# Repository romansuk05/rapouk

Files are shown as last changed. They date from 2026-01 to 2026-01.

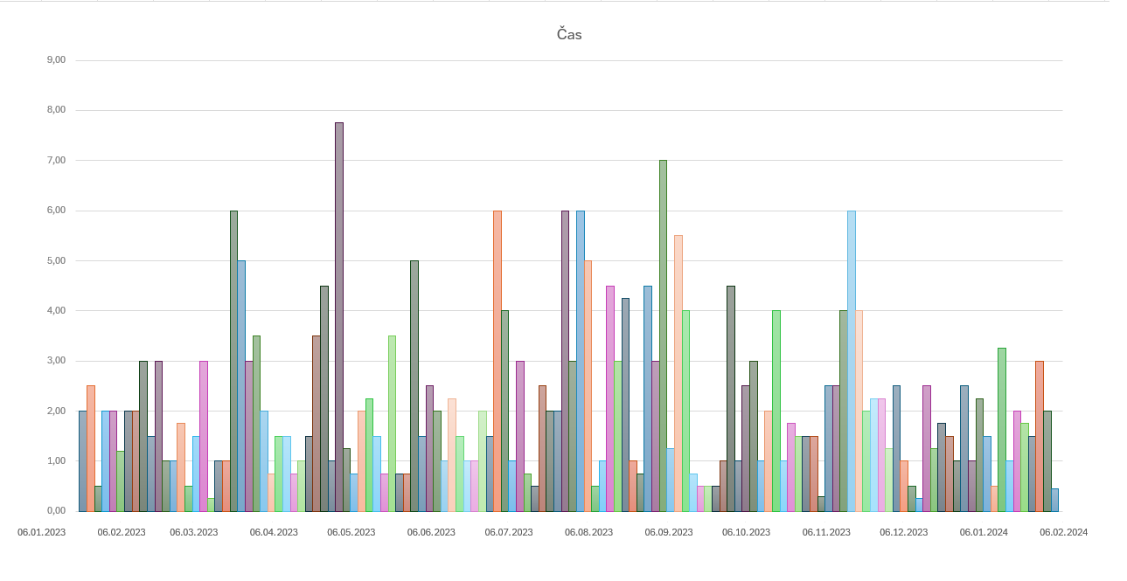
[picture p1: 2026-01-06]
Datasheet and pics/Graf.png

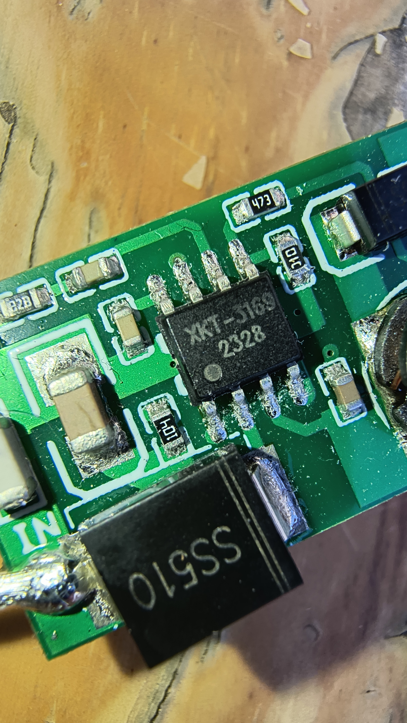
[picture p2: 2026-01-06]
Datasheet and pics/IMG_20240922_112600092_HDR.jpg

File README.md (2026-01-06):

<h1>Project Rapouk</h1>

<p>Hello, this project I made on highschool as final project. Rapouk is quadruped robot. I made it from aluminium on DIY mill, ESP32 and custom PCB. There should be everything which you should need for assembling your Rapouk. Evethought everything is in czech language, so use some translator for this xD</p>
<p>Also there are my thesis with everything that I done in this project</p>
<p>This depo is unsorted af so GL&HF with finding something xD</p>
<p>It is completly open source, so create another versions of this spider</p>
<p>There are some interesting links with this project:</p>
<p>https://www.youtube.com/watch?v=WBYnp2NAGiE</p>
<p>https://www.instagram.com/romansuk05/reel/DLpOciDirai/</p>

<p>Enjoy your journy with Rapouk!</p>





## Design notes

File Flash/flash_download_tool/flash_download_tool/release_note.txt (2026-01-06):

3.9.8：
* add UI to support flash & efuse read
* support ESP32-C5 / ESP32-C61

3.9.7：
* support ESP32-P4
* update UI display icon
* Fix bug: icon stuck after long-term use

3.9.6：
* support ESP32/ESP32H2/ESP32C6/ESP32C2/ESP32S2 secure boot version2 and flash encryption
* config DUT number in multiconfig file ,up to 20pcs
* update secure config file, see docs in detail

3.9.5：
* support esp32-h2
* support erase button disable
* fix some bugs

3.9.4：
* support esp32-c6
* support esp32-c3/esp32-s3 flash encrytion
* add xmc flash fix
* support dut count in factory mode

3.9.3:
* support esp32-c2
* update finish UI show

3.9.2:
* fix configure file error
* update autostart process

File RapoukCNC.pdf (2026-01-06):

Vyšší odborná škola, Střední průmyslová škola a Obchodní akademie,

### Čáslav, Přemysla Otakara II. 938

# ROČNÍKOVÁ PRÁCE

2024 | Roman Suk

Vytvoření základní konstrukce robotického pavouka včetně dokumentace a vizualizace.

Čestné prohlášení

Místopřísežně prohlašuji, že jsem svou ročníkovou práci vypracoval samostatně a použil

jsem pouze podklady (literaturu, projekty, SW atd.) uvedené v seznamu vloženém v práci.

Prohlašuji, že tištěná verze a elektronická verze práce jsou shodné.

V | , dne | | |
| podpis

Poděkování

Děkuji vedoucímu práce Ing. Františkovi Obešlu a oponentovi práce Ing. Janu

Novákovi. Dále Mgr. Karlu Kvapilovi, Bc. Matěji Reichmannovi, Ing. Karlu

Mlčochovi, Ing. Vlastimilovi Andrlemu a v neposlední řadě i třídnímu učiteli Ing.

Davidu Němcovi MBA, a zejména svým rodičům za obětavou pomoc a podnětné

připomínky, které mi během práce poskytovali.

Anotace

Cílem této práce bylo vytvořit konstrukci robotického pavouka. V průběhu práce probíhal

výpočet a výběr materiálu. Práce se dále zaobírá stavbou CNC stroje, svařováním hliníku

a skládáním pavouka samotného.

Klíčová slova

Robotika, pavouk, konstrukce, hliník, CNC, programování, sváření

Annotation

The main focus of this coursework was to create body of robotic spider. There was

materiál selection and calculation. Next focus was building of the CNC machine,

aluminium welding and assembly of the spider itself.

Keywords

Robotic spider, construction, aluminium, CNC, programming, welding

## Obsah

## 1 Úvod

V dřívějších dobách, kdy jsem si hrál s RC modely, mě mrzela jedna věc a to, že ke

každému modelu byl potřeba přesný ovladač. Dražší modely už měly univerzální, ale ty

jsem neměl. Občas ani nebyla možnost, v případě ztráty nebo rozbití ovladače,

komunikační jednotku vyměnit.

Největším paradoxem je, že dnes všichni disponujeme univerzálními ovladači, se kterými

se lze připojit k internetu. Ano – telefon, tablet, nebo i počítač. Tak proč nevyužít tyto

technologie?

S tímto mě vždy fascinovaly neobvyklé platformy robotů. Kreativita, projekt, mechanika

a vše, co za těmito speciálními projekty stálo. Z toho důvodu jsem zvolil platformu

pavouka. Vybral jsem si pavouka se čtyřma nohama, protože má menší počet

servomotorů a baterie bude mít delší výdrž. Nadále jsem měl myšlenku, zda se bude můj

„pavouk“ pohybovat jako pavouk (tělo je při pohybu ve stejné výšce), nebo jako klasické

čtyřnohé zvíře, co svým tělem kolíbá.

Celý projekt jsem pojmenoval pod názvem Rapouk. Název vznikl spojením slov robot a

pavouk.

## 2 Prvotní konstrukce

Tento projekt jsem chtěl vytvořit již před lety. Z toho důvodu už jsem měl vytištěné 3D

modely z internetu. Bohužel už nejsem schopen najít zdroj, odkud jsem v té době čerpal.

V úložném boxu s různými 3D modely jsem našel tyto vytištěné součásti a použil je pro

prvotní seznámení s pohybem.

## 2.1 Programování pavouka

První nápad mě inspiroval v přírodě. Zanalyzovat videa pavoučích pohybů a vytvořit

stejné pohybové algoritmy, které nám jsou dostupné ve volné přírodě. Bohužel v přírodě

neexistuje žádný pavouk se čtyřma nohama.

Vycházel jsem z videí různých pohybů těchto pavouků na internetu. Následně jsem si

vytvořil vlastní algoritmy pohybů, se kterými budu vylepšovat finální model. Nechtěl

jsem nejdříve modelovat a následně programovat, protože jsem nevěděl, na které

problémy narazím. Tento krok mi ušetřil mnoho času a pomohl mi s vylepšením budoucí

konstrukce (viz Tření). (1) (2) (3) (4) (5)

## 2.2 Tření

Při prvním vytváření algoritmů jsem narazil na problém se třením. Na hladkém stole, na

kterém pracuji, konstrukce vysloveně klouzala. Nedokázala se hýbat, protože měla

nízkou hmotnost a nevytvořilo se dostatečné tření, aby se rozpohybovala. Při tomto

testování byla konstrukce z ABS plastu.

## 2.3 Výpočty

V rámci této práce jsem prováděl výpočet zatížení na ohyb v MS Excel. Počítal jsem

nestandartním způsobem, kdy počítám s redukovaným maximálním napětím. To

znamená, že využívám určité procento maximálního napětí, čímž dochází

k předimenzování. Vyšlo mi, že při 10 % maximálního napětí na ohyb servomotor udrží

12,5 N neboli 1,25 kg (viz Příloha EE). Využíval jsem data z datového listu od

servomotoru SG90 9 g, který má vytvořená převodová kola z nylonu. (6) (7)

## 3 Tvorba konstrukce

## 3.1 3D tisk

Při vytváření modelů jsem se inspiroval různými konstrukcemi z internetu. Po analýze

nápadů a provedení od ostatních tvůrců jsem začal modelovat svého pavouka. (1) (2) (3)

(4) (5)

Modely, které jsem vymodeloval s přesným rozměrem, jsem vytiskl na 3D tiskárně a

zkontroloval. Zjistil jsem, že z důvodu tepelné roztažnosti, jsou rozměry jiné. U menších

rozměrů (do 5 mm) byl rozdíl 0,3 mm. U větších, číselně (od 20 mm) byl rozdíl okolo

0,7 mm. Model jsem v programu Autodesk Inventor zvětšil o rozdíl, aby vytisknutá část

pasovala přesně do uložení.

Po konzultaci s vedoucím práce jsem zjistil, že se model nerozšiřuje v modelovacím

programu, ale ve sliceru před tiskem. Hodnoty jsem vrátil na původní a vytiskl

standartním způsobem.

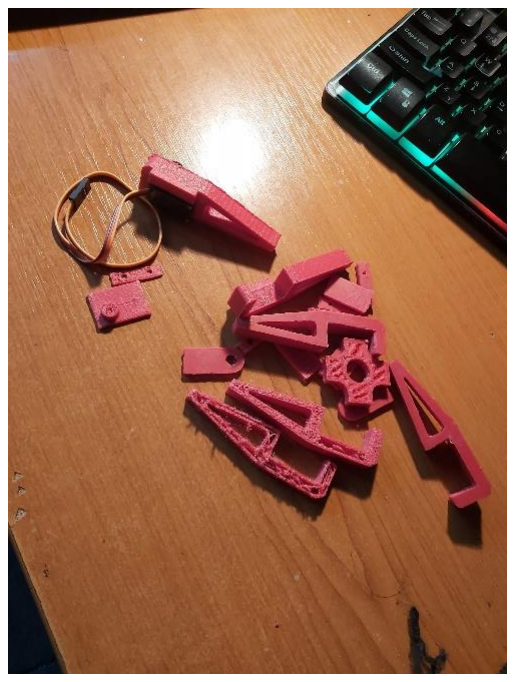
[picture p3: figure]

Obrázek 1 - 3D modely konstrukce

## 3.2 Konstrukce z hliníkové slitiny

Plastové konstrukce jsem tvořil již dříve. Mým hlavním záměrem bylo tento projekt

vylepšit a obohatit o něco nového. Zalíbila se mi myšlenka použití kovů. Vybral jsem si

hliníkovou slitinu – je levná, lehká, dostupná, však složitá na obrábění, pokud nebude

chlazena správnou kapalinou.

Původně jsem chtěl odlévat a použít hliníkové plechovky od sycených nápojů. Po zjištění

komplikovanosti technické dokumentace jsem se rozhodl obrábět z normalizovaného

polotovaru. Zbytečně bych ztrácel čas, protože samotné odlití by nebylo tak časově

náročné jako tvorba technické dokumentace odlitků.

V domácím skladu jsem našel ploché profily o tloušťce 10 mm, 5 mm a 3 mm. Přesně ty,

které jsem potřeboval. Tímto jsem mohl začít obrábět. Jedná se o materiál ENAW-6060

T6 (AlMgSi0,5). Zmíněný materiál má průměrné technologické vlastnosti a lze ho použít

téměř při jakékoliv zpracování. (8)

Obrázek 2 – Polotovary z hliníkové slitiny

Nejdříve jsem si vytvořil rýsovací jehlu, protože v dílně nebyla žádná k nalezení. Vytvořil

jsem ji z kulatého pilníku. Následně jsem nalepil výkres na kovový profil pomocí

klasického lepidla Herkules a začal vše obkreslovat (viz Obrázek 3 - Příprava ručního

obrábění, strana 14).

Připravil jsem si přímočarou pilu s plátkem určeným na hliník a jeho slitiny. Jako první

jsem začal obrábět základní rám pavouka. Ten je určen pro montáž motherboardu,

akumulátoru a dalších potřebných součástí. Strávil jsem nad tím mnoho času s relativně

nepřesným výsledkem. Proto nastal čas nasadit stroje!

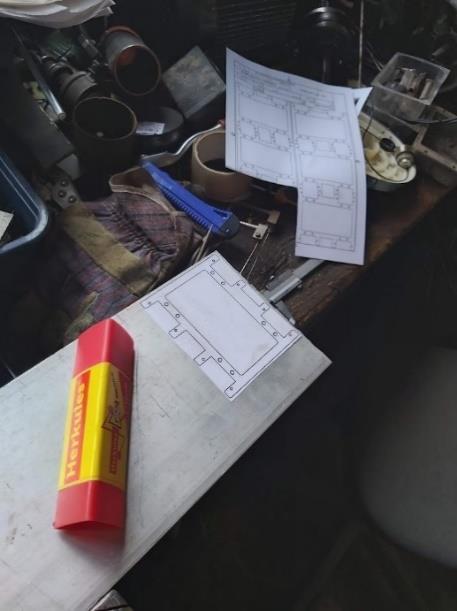
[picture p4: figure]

Obrázek 3 - Příprava ručního obrábění

## 3.2.1 Další materiály

V rámci správné analýzy jsem se rozhodoval i nad ostatními materiály.

### 3.2.1.1 Ocel

Kvůli dobrému obrábění jsem mohl využít ocel. Přesněji pásové nebo plechové

polotovary. Jedna z největších záporných vlastností ocelí je koroze. Proto jsem nad tímto

materiálem dále neuvažoval. Sice všechny faktory splňuje, ale zde musím použít materiál,

který nekoroduje.

### 3.2.1.2 Nerezová ocel

Ocel, která nekoroduje zní jako ideální materiál. I přes vynikající vlastnosti jsem si

nerezovou ocel nevybral, protože bych ji musel nakoupit. Zatímco vybrané hliníkové

polotovary jsem měl ve skladu s plným rozsahem použití a rozměrů.

### 3.2.1.3 Titanzinek

Titanzinek byl pro mě absolutně neznámý materiál. První, co jsem uviděl byla cena, která

byla hodně vysoká. To by mi tento projekt dost prodražilo, proto jsem tento materiál dále

ani nezkoumal.

## 4 CNC

Přiznám se, jsem líný člověk, který si chce vše zjednodušit. Proto jsem začal s opravou

staré CNC frézky, která fungovala ještě na MS-DOS. To jsou doby Windows 95, 98, až

XP. Takže tato frézka je starší, jak většina aktuálních studentů na naší škole (k roku

2023/24).

Obrázek 4 - Ruční obrábění

Začal jsem vyčistěním pomocí stlačeného vzduchu z kompresoru, následně pomocí

navlhčeného kusu látky. Závity s kolejnicemi, na kterých se posouvá fréza, jsem pročistil

a namazal pomocí přípravku WD40 a jeho náhražky od W5. Stroj jsem vyčistil pomocí

čističe na brzdy. Též jsem musel rozebrat a očistit krokové motory, protože rotor byl

přirezlý ke statoru, k čemuž jsem použil brusný papír o hrubosti 240. Následně jsem

vyměnil sloupečky, na kterých je upevněn posuvný motor, ale chyběla jedna věc – u CNC

stroje byla pouze jedna zubová spojka, a proto jsem je musel vyrobit. Celkově jsem

potřeboval čtyři spojky. Použil jsem opět program Autodesk Inventor. Spojky

vymodeloval, vytiskl na 3D tiskárně a pilníkem poupravil, aby fungovaly jako originální.

Ano, mohl jsem zvolit i jiné způsoby, jsem lenošná osoba, a proto jsem nechal výrobu na

dalším CNC stroji.

Obrázek 5 - Nálezový stav CNC frézky

## 4.1 Posuvný vozík na CNC frézku

Celý stroj jsem položil na konstrukci s kolečky, která mi tvořila velice dobrý stůl. Celou

CNC frézku jsem měl v perfektní výšce na čistění a operace. Na spodek konstrukce jsem

provizorně vložil sololitovou desku, abych si mohl odkládat věci.

Díky tomuto vozíku jsem se mohl s celým strojem pohybovat po dílně prakticky

kamkoliv. Též jsem ocenil kolečko se zašlapávací brzdou, aby se stroj nemohl pohybovat.

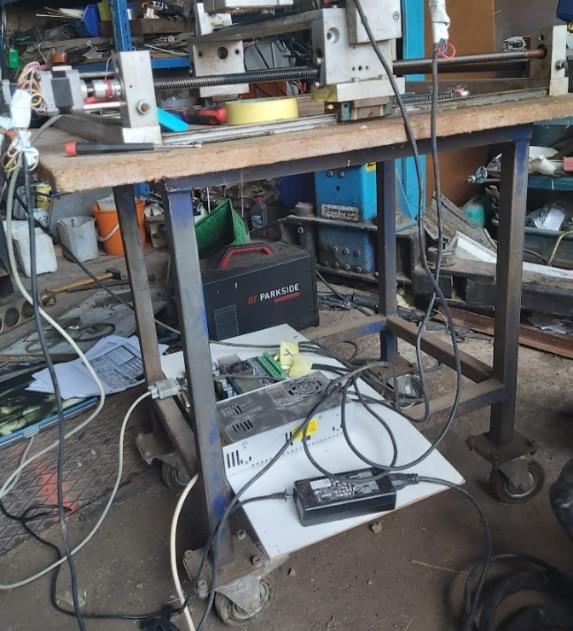
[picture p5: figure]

Obrázek 6 – Provizorně vložená sololitová deska

## 4.2 Elektronika

Původní elektronika byla v plastové krabici, která v sobě měla zdroj, připojení pomocí

LPT a připojení pro krokové motory pomocí sériového portu. Na neštěstí jsem nebyl schopen najít vhodné nastavení, a ani se mi ho nepodařilo vytvořit. Čekala mě výměna

elektroniky. Jako řadič jsem použil čtyřosý řadič TB6560, jenž jsem připojil k 12 V

zdroji, který dokázal pohánět proudem stroj až 5 A. Celkově zdroj dokázal produkovat

60 W elektrické energie. Ke zdroji jsem připojil také připojovací šnůru do zásuvky na

230 V.

Po hodinách zkoušení jsem narazil na stejný problém. Motory vydávaly zvuk, však

nehýbaly se. Hledal jsem a zkoušel různé možnosti nastavení, ale nic se mi nepodařilo

zprovoznit. Takže jsem vyzkoušel ostatní desky s označením TB6560. Mnoho jich

nefungovalo, ale pětiosý řadič začal fungovat. Dokonce jeden řadič shořel.

Vše jsem zapojil, připojil původní ruční ovládání a vše začalo fungovat. Vyzkoušel

všechny osy a nastavil motory na řadiči. Ještě jednou pročistil všechny kolejnice a matice,

které byly znečištěné od dřívějšího používání.

Obrázek 7 – Ilustrační fotka ovládací desky a zdroje

## 4.2.1 Nastavení elektroniky

K mé ovládací desce naštěstí existoval datový list. Tím jsem zjistil nastavení daných

spínačů. V komunitě lidí, kteří se věnují domácím CNC strojům je tato elektronika velice

oblíbená. S hledáním dodatečných informací jsem neměl problém. Především jsem hledal

v manuálu na komunitních stránkách. (9)

Celkově pro jeden krokový motor je jeden DIP spínač se šesti pozicemi.

### 4.2.1.1 Nastavení proudu

Prvními dvěma pozicemi se nastavuje maximální proud pro jednotlivý výstup motoru

ovládací desky. Toto nastavení jsem nastavoval dle zahřívání a výkonu krokového

motoru. Původní motory neměly dostatečný výkon. Při otočení se velice zahřívaly. Přesně

toto nesmí nastat.

Pozice 1 | Pozice 2 | Maximální proud
Zapnuto | Zapnuto | 100 %
Zapnuto | Vypnuto | 75 %
Vypnuto | Zapnuto | 50 %
Vypnuto | Vypnuto | 25 %

Tabulka 1 - Nastavení proudu (9)

Se silnějšími motory jsem využíval 75 % maximálního proudu.

### 4.2.1.2 Nastavení mikrokrokování

Pátou a šestou pozicí se nastavuje rozložení kroku na více menších kroků, tzv.

mikrokroků.

Pozice 5 | Pozice 6 | Rozdělení kroku
Zapnuto | Zapnuto | 1
Zapnuto | Vypnuto | ½
Vypnuto | Zapnuto | ⅛
Vypnuto | Vypnuto | ¹⁄₁₆

Tabulka 2 - Nastavení mikrokrokování (9)

### 4.2.1.3 Nastavení vybíjení

Toto nastavení jsem moc nenastavoval a nechal na základní pozici. Ovládá se třetí a

čtvrtou pozicí DIP spínače.

Pozice 3 | Pozice 4 | Mód
Zapnuto | Zapnuto | Rychlé
Zapnuto | Vypnuto | 25 %
Vypnuto | Zapnuto | 50 %
Vypnuto | Vypnuto | Pomalé

Tabulka 3 - Nastavení vybíjení (9)

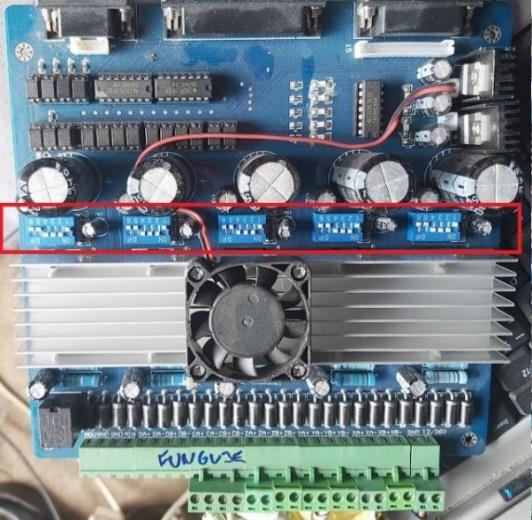
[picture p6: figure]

Obrázek 8 - Nastavení ovládací desky

## 4.3 Vřeteno

Originální vřeteno jsem na stroji neměl. Použil jsem tedy jiné vřeteno na 48 V. Dokonce

k němu bylo i přesné uložení pro tento motor.

Původní uložení na frézce mělo menší rozteč děr, takže bylo potřeba vyvrtat nové díry. Z

důvodu nedostatku místa ze zadní části, kde byl hlavní nosník osy Y, jsem musel vytvořit

závity M6. Do těchto závitů se zašroubovala závitová tyč, která sloužila stejně jako

svorník. Jednalo se o nejjednodušší řešení, protože bych musel frézovat otvory pro

uložení hlavy šroubu s vnitřním šestihranem.

U oceli by to nebyla veliká problematika, ale u hliníkových profilů jsem, z důvodu

nízkých zkušeností, použil tento postup. Dodnes ani nevím, zda ve výbavě mám

záhlubník pro vytvoření otvorů pro hlavu šroubu.

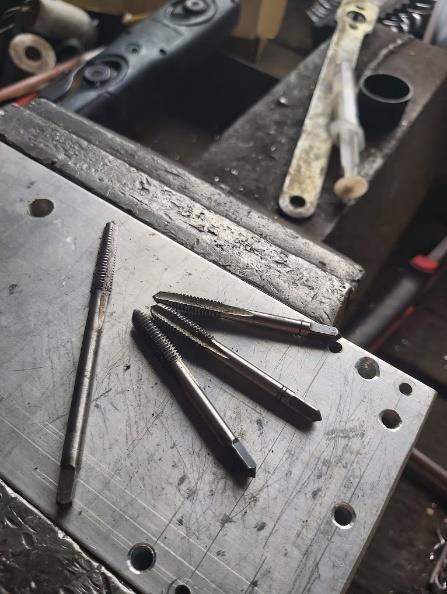
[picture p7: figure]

Obrázek 9 - Závitníky

Závitové tyče jsem zalepil pomocí přípravku Loctite. Na závitové tyče jsem vložil uložení

vřetena, které jsem utáhnul kuželovými maticemi. Tyto matice mi vyrobil otec. Do

sklíčidel vrtačky jsme uchytili závitovou tyč, na kterou jsme našroubovali dlouhou matici.

Matice byla zbroušena na kotoučové stolní brusce. Tím jsme vytvořili kuželovou

charakteristiku.

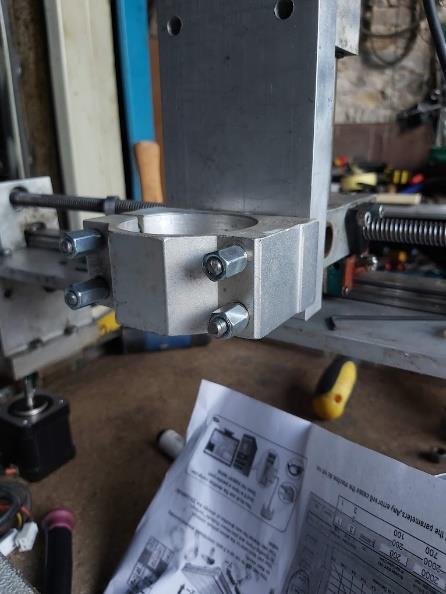
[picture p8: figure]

Obrázek 10 - Uložení vřetena

Kuželovitost jsme využili z důvodu přesného uložení a vycentrování. Díky tomu matice

držely uložení vřetena rovnoměrně.

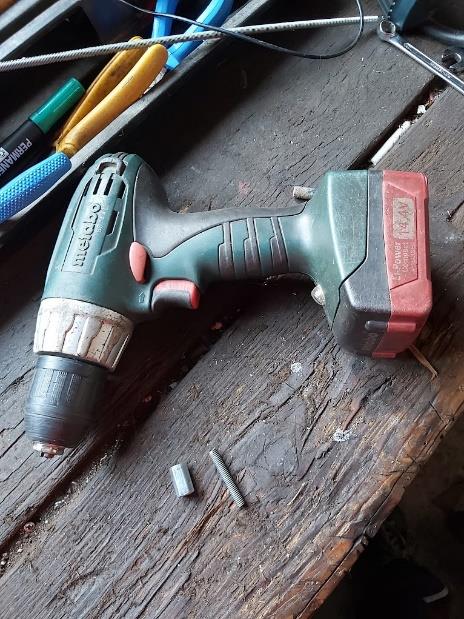
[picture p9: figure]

Obrázek 11 - Výroba kuželové matice

Následně jsem vše připravil a přišrouboval na stroj.

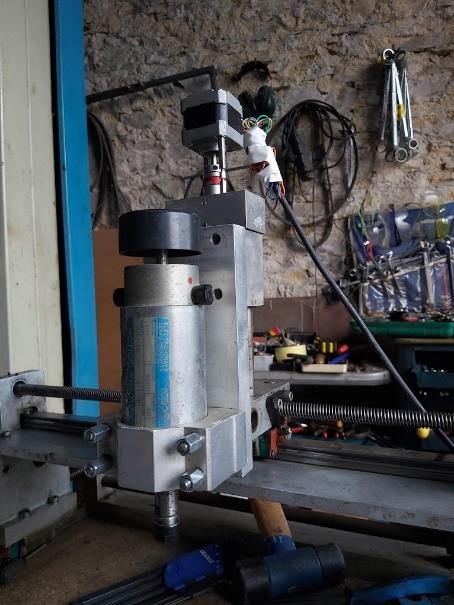
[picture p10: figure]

Obrázek 12 - Vřeteno

## 4.3.1 Kabely k vřetenu

O vřetenu samotném nemám moc informací a špatně se hledají. Neznám ani maximální

proud, a proto musím improvizovat. Ve skladu jsem našel rozebraný podlahový mycí

stroj, který fungoval na akumulátor. Využil jsem silné kabely, které byly dlouhé. Na jeden

konec kabelu jsem připojil konektor pro připojení motoru. Konektor zaletoval a ochránil

smršťující bužírkou vůči zkratu.

Při zkompletování kabelů jsem použil další zdroj na 48 V, ke kterému jsem připojil

přívodní šnůru s ochranou. Ještě jsem použil model ochranné krytky, kterou jsem stáhl

z internetu a vytiskl na 3D tiskárně. (10) Zabraňuje dotyku s 230 V. Teoreticky by zde být nemusela, avšak z vyššího napětí jak 50 V mám obavy, a proto z důvodu bezpečnosti

tuto krytku sem přidávám.

Obrázek 13 - Krytka zdroje

Bohužel při zkoušce pohybu s osami jsem zjistil, že kabely jsou, i přes jejich délku, moc

krátké. Měl jsem dvě možnosti. Najít, nebo koupit jiné, anebo zmenšit vzdálenost mezi

zdroji a krokovými motory s vřetenem. Nejrychlejší řešením bylo zmenšení vzdálenosti.

Obrázek 14 - Krytka upevněna na zdroji

## 4.3.2 Změna polohy řídící části CNC stroje

Potřeboval jsem celou řídící část posunout co nejvýše. Řídící částí míním tu část, která

měla sloužit pro odkládání nářadí (viz Obrázek 6 – Provizorně vložená sololitová deska,

strana 16). Změřil jsem si výšku zdroje, která byla 50 mm. Proto jsem zvolil jako

dostatečnou mezeru 80 mm.

Mezi zbytky materiálu jsem našel L profily s podélnými dírami. Délkově měly přesah

necelých 40 mm. Díry a délka profilu mi přesně vyhovovaly.

Do konstrukce s kolečky jsem vyvrtal díry o průměru 4,8 mm. Předvrtal jsem díru o

průměru 2,2 mm a následně průměr zvětšoval. Vše jsem vrtal akumulátorovou vrtačkou od firmy Metabo. Vzdálenost od horního nosníku byla 100 mm. Profily jsem přinýtoval

pomocí krátkých nýtů s širokou hlavou a použil ruční nýtovací kleště. Ruční kleště mi

daly zabrat, protože drtivou většinu času jsem nýtoval s pneumatickými nýtovacími

kleštěmi.

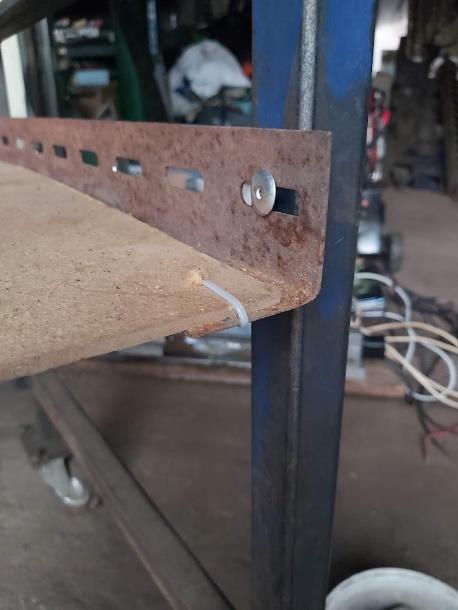
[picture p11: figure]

Obrázek 15 - Přinýtovaný L profil

Nejdříve jsem pracoval se špatnými nýtovačkami, které byly vyrobeny na kratší hřebíky,

a proto se mi zasekávaly a nenýtovaly. Po výměně jsem mohl v nýtování pokračovat.

Bohužel po nýtování se mi hřebíky přetrhly ve špatném místě. Proto jsem vzal silné a

přepákované štípací kleště, kterými jsem tuto nedokonalost vyřešil.

Následně jsem vložil původní sololitovou desku do L profilů. Ještě jsem použil vodováhu,

zda profily nejsou přinýtovaný špatně, popřípadě křivě. Vodováha mi ukázala perfektní

vodorovnost.

Obrázek 16 - Vodováha

Sololitovou desku jsem ještě připevnil ke konstrukci pomocí stahovacích pásků. Nejdříve

jsem vyvrtal díry a následně spojil.

Vše z řídící části jsem rozebral a složil zpět, aby se mi zbytečně nekřížily kabely mezi

sebou. Jako poslední krok jsem kabely seskládal a spojil opět stahovacím páskem ke

konstrukci.

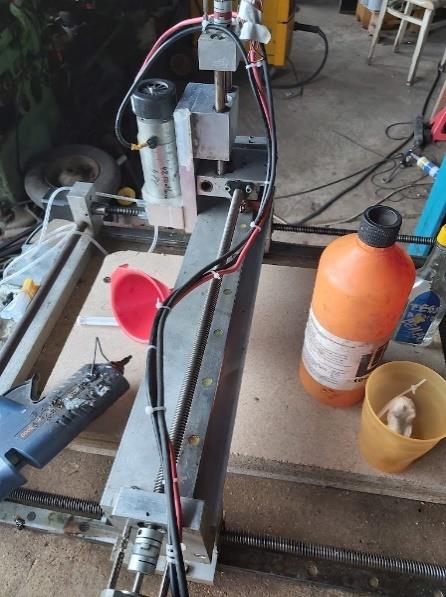
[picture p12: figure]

Obrázek 17 - Osa Y

## 4.4 Motory

Originálně na této frézce byly použity krokové motory Microcom SX17-0804. Na Ose Y

a Z fungovaly dobře, na osu X již nestačily.

Proto bylo potřeba vylepšení s výkonnějšími motory. Použil jsem LDO-42STH47-

1684AS, který disponuje dvakrát větší cívkou.

Obrázek 18 - Krokové motory

## 4.4.1 Uložení motoru

S větším motorem nabývá i samotná váha. Původní uložení, které bylo vytvořeno z

distančních sloupků, by motor neudrželo. Distanční sloupečky jsem odmontoval a využil

vytvořeních závitů ve stavební kostce, kde byl původní motor. Tyto motory měly stejnou

rozteč šroubů, takže zde nebyl žádný problém k vytvoření tohoto uložení.

S tímto uložením přišly první výdaje. Ve skladu jsem neměl tak dlouhé šrouby, které bych

mohl použít na uložení motoru. Proto jsem si nechal objednat šroub s válcovou hlavou a

vnitřním šestihranem M3-60 DIN 912 ZB 8.8, které jsem následně zkrátil na 55 mm.

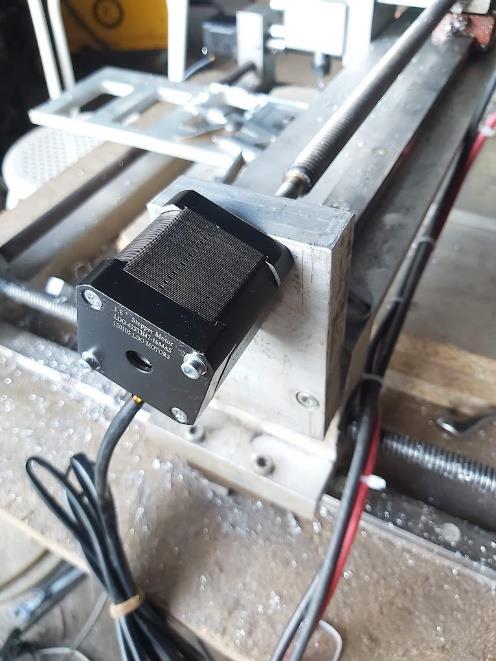
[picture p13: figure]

Obrázek 19 - Krokový motor na ose Y

Při skládání jsem pod hlavu šroubu použil podložku a vše sešrouboval k sobě.

## 4.4.2 Připevnění uložení motoru k nosné desce CNC

## stroje

Připevnit uložení motoru bylo poměrně obtížné. Nosná deska je z dřevotřísky. Jelikož o

stroj nebylo staráno a bylo ve vlhkém prostředí, tak došlo k její deformaci. Naštěstí se

nejedná o velké zkroucení, však o ztrátu pevnosti.

Při připevňování deska nedokázala udržet tlak hlavy šroubu. Pod tlakem hlavy šroubu se

začala drolit a ztrácet pevnost. Z tohoto důvodu jsem použil podložky o velkém vnějším

průměru, abych rozložil tlak při utahování. Tím by hlava šroubu nevytvářela deformace.

Podložky jsem použil M8/9x28-3 mm DIN 440R A2.

Musel jsem vyměnit i samotné šrouby. Původní konstrukce počítala s uložením hlavy

šroubu v nosné desce. Toto uložení jsem nemohl použít. S použitými podložkami šrouby

byly moc krátké. Vyměnil jsem je za delší se stejným průměrem 8 mm neznámé normy.

Celková cena spojovacího materiálu byla 220 Kč včetně DPH.

## 4.4.3 Spojení závitové tyče a motoru

Jeden z mála rozdílů těchto krokových motorů byl průměr hnací hřídele, která z motoru

vycházela. Rozdíl byl u původních 5 mm a nových 6,3 mm. Původní spojení hřídelí bylo

pomocí axiální spojky. Neměl jsem žádné spojky, které by se daly použít. Mohl jsem tuto

spojku koupit, avšak cena těchto spojek, i na východních e-shopech, je vysoká.

S touto spojkou mi pomohl otec. Využili jsme kulatou tyč o průměru 23 mm neznámé

oceli. Tyč jsme uřízli na délku 30 mm a na soustruhu provrtali vrtákem o průměru 6,3 mm

a z opačné strany o průměru 8 mm. Jako pojistné šrouby jsme použili stavěcí šrouby

s vnitřním šestihranem o průměru 5 mm a stoupáním 0,8 mm.

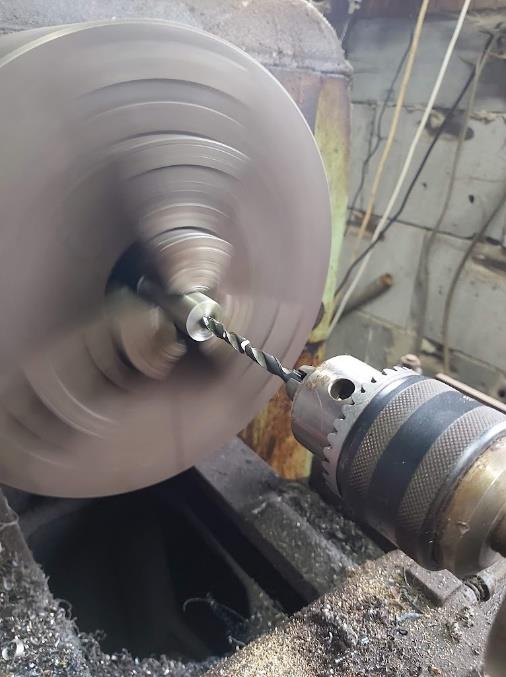
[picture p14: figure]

Obrázek 20 - Soustružení

Spojky jsme nainstalovali na stroj a svoji funkci plnily stoprocentně. Nejdříve jsem se

obával špatného vyvážení nebo vyvrtání spojky. Kdyby spojení nebylo v ose, mohlo by

dojít ke špatnému posuvu stroje.

Tímto bodem byla HW část CNC stroje hotová.

Obrázek 21 - Spojka na ose X

## 4.5 Nástroje pro obrábění

Fréz jsem za život měl v rukách poměrně málo, natož na hliníkové slitiny. Drtivá většina

těchto fréz má průměr okolo 2 mm. Tento průměr je dost malý a to nepočítám, že toto

jsou mé první zkušenosti s CNC frézkou. Bohužel i průměr sklíčidla je malý a to pouze

3,125 mm (3 a ⅛ mm).

Jsem začátečník a v budoucnu nepřepokládám, že budu denně obrábět pomocí fréz.

Z tohoto důvodu jsem se rozhodl nakoupit levné frézy. Objednal jsem je z čínského webu

www.aliexpress.com. Celkově pět fréz na hliník o zmíněném průměru.

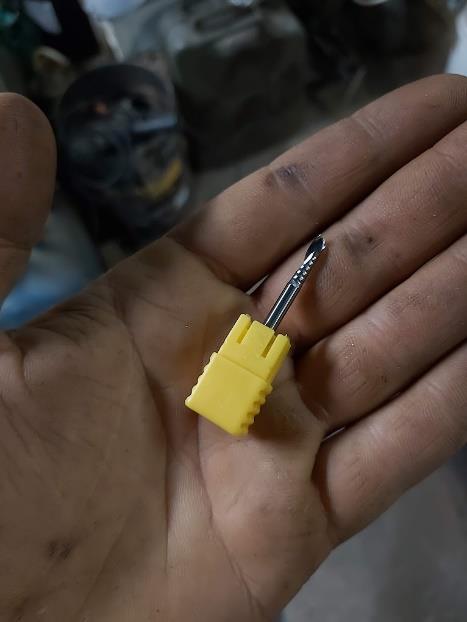
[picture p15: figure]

Obrázek 22 - Fréza o průměru 3,175 mm

Cena těchto fréz byla 16,7€ (necelých 400 Kč) včetně dopravy a DPH.

## 4.6 Testování a kalibrace stroje

Po složení CNC stroje nezbývá nic jiného než testovat. Tato část je důležitá kvůli

samotnému chodu stroje. Při testování jsem zpozoroval, že se stroj lehce zasekává.

Především na ose X, kde jsou uloženy dva motory. Snažil jsem se tento problém vyřešit

zvýšením maximálního proudu. Tímto krokem motory byly hlasitější a vytvářely více

tepla. Proto jsem nastavení vrátil zpět na 50% maxima.

Obrázek 23 - Finální CNC frézka

## 4.6.1 Mazaní

Jedno z dalších řešení nízkého výkonu motorů je mazání. Mazáním lze vytvořit na film,

kterým lze docílit snížení třecí síly na povrchu namazaných částí. Tímto jevem získáme

nižší energetickou náročnost.

K vyčištění jsem používal přípravky WD40 a přípravek na mazaní od W5. Nevýhoda

těchto přípravků je v odpařování. Proto jsem pro dlouhodobé mazání použil grafitovou

vazelínu. Ta se používá prakticky kdekoliv. Osobně jsem se setkal i s mazáním pásů u

rypadla.

Obrázek 24 - Maznice s vazelínou

Vazelínu jsem aplikoval pomocí maznice ve vozících na kolejnicích, které vozí a

podepírají osy. Na závitové tyče jsem použil též grafitovou vazelínu s Interflonem.

Obrázek 25 - Interflon

## 5 Ovládací CNC SW

Dnes je drtivá většina obráběcích SW s licencí. Samozřejmě výjimka potvrzuje pravidlo

a jsou tu i programy, které jsou zdarma a pro “hobby“ použití. Jejich největší nevýhodou

je zastaralost, protože byly vytvořeny v dobách od MS-DOS až po Windows XP. Též je

potřeba počítač s LPT portem, který je velikou vzácností. Tento port se dnes nevyužívá.

## 5.1 Mach3

Mach3 je program volně ke stažení, který lze používat na OS Windows 95 až Windows

XP. Je velice jednoduchý na ovládání, přestože je lehce nepřehledný.

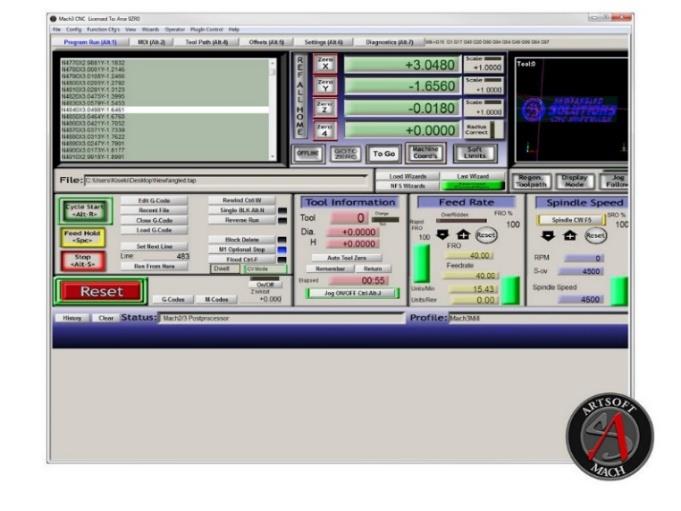
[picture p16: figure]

Obrázek 26 - Mach3 (11)

Bez dokumentace k řídící desce prakticky nelze program použít. Počítač, který skrze LPT

port ovládá CNC stroj, vysílá pulzy na dané piny. Bez správného nastavení pinů nepřijde

informace na určité místo a stroj nebude fungovat. (12)

Následně po nastavení komunikace se musí nastavit motory. Je zde celkově pět políček

pro nastavení.

## 5.1.1 Step per

Step per nastavuje počet kroků krokového motoru na otáčku. Jednoduchým výpočtem si

dokážeme krok na otáčku vypočítat. Tento výpočet lze aplikovat pouze na pojezdech na

závitových tyčích. Pokud by se pro pohyb použily řemeny, tak výpočet bude jiný.

počet kroků na otáčku ⋅ počet mezikroků stoupání

= step per

Rovnice 1 - Výpočet step per (13)

Počet kroků na otáčku vypočítáme pomocí úhlu na krok. U mého krokového motoru je to

je 1,8°.

360

o
1,8

o = počet kroků na otáčku

360

o
1,8

o = 200

Z rovnice lze usoudit, že pro jednu celou otočku musí motor udělat 200 kroků.

Stoupání je myšleno stoupání na závitové tyči, na které se celá osa unáší. Na mém stroji

byly závitové tyče se stoupáním 5 mm.

Mezikrok nám rozděluje samotný krok na více kroků, takzvaných mezikroků. Mezikroky

zvýšíme rozlišení stroje, takže bude větší přesnost a plynulost. Nevýhoda mezikroků je

vyšší spotřeba energie.

200 ⋅ 8
5

= 320

Z dosazení do vzorce vidíme, že do kolonky „Step per“ zadáme hodnotu 320. Tento

vzorec jsem odzkoušel a stroj jsem nechal zkalibrovat v SW. Vše vyšlo přesně dle

výpočtů.

## 5.1.2 Rychlost a zrychlení

Velocity je maximální rychlost, kterou se motor bude pohybovat. Acceleration je

akcelerace motoru. Tímto nastavujeme pohyby krokových motorů. Jednotky se udávají

v mm×s

-1
a mm×s

-2

V programu vidíme křivku zrychlení a zpomalení, která se jmenuje rampa. Program ještě

dopočítává přetížení v jednotce G.

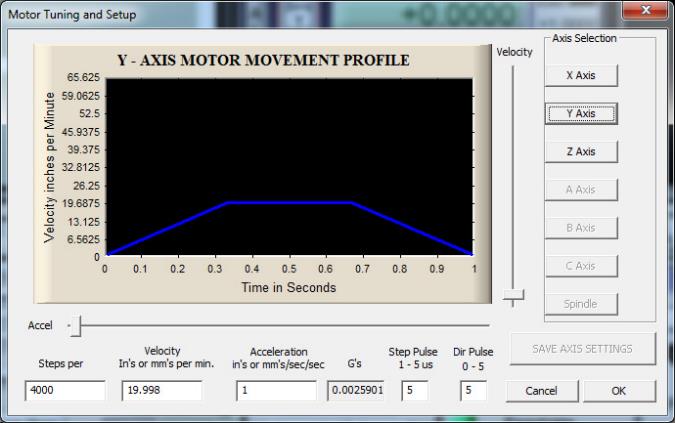
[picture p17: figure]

Obrázek 27 - Mach3 rampa (14)

Při poslechu jiných CNC strojů slyšíme identické pískání a bzučení krokových motorů.

Tohoto zvuku chceme při nastavování docílit.

## 5.1.3 Step a Dir puls

Tyto hodnoty nám nastavují minimální puls, který dokáže řadič zachytit. Toto nastavení

jsem nechal na základním nastavení.

## 5.1.4 Problematika komunikace nových OS

Program jsem nejdříve vyzkoušel na novějším systému Windows 7. Po nízkých desítkách

hodin se mi stroj nepodařilo zprovoznit. Fungoval velice slabě na nesmyslné nastavení

(viz Step per, strana 30). Po uložení nastavení se ukončila komunikace.

Celý problém byl v operačním systému. Používal jsem Windows 7, namísto XP a starších.

Přesně nevím, jakou změnu Microsoft udělal s LPT porty. Kdybych chtěl používat

novější OS, tak bych musel použít převodník za nízké tisíce korun. Proto byla lepší

možnost přeinstalovat počítač na starší verzi Windows.

Po nainstalování Windows XP vše fungovalo. Celý stroj mi fungoval prakticky hned.

## 5.2 Step-Four

Step-Four je program, který se používal už na základním MS-DOS. S MS-DOS mi

pomohl otec, který v DOS dříve pracoval. K jeho zprovoznění bylo potřeba přihlášení s

hardwarovým klíčem, který odesílal data do CNC stroje. Stejně jako Mach3 byl připojen

pomocí LPT portu.

Tento program jsem si moc neozkoušel, protože mi jako první začal fungovat Mach3.

Každopádně prostřední S4 bylo velice retro. Typický retro kostičkovaný design jako mělo

logo od MS-DOS.

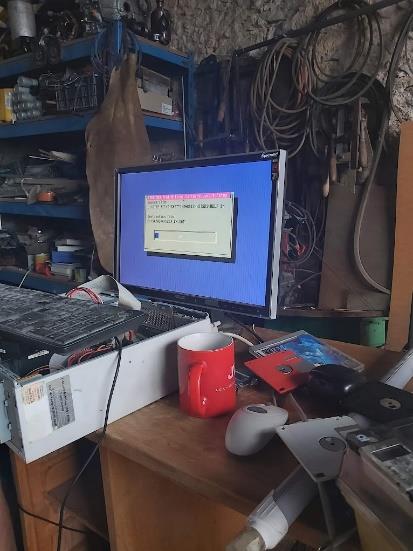
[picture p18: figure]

Obrázek 28 - MS-DOS

## 6 CAM

CAM je nedílná součást CNC strojů, pokud nechceme psát program ručně. Jelikož mi

přijde nesmyslné, abych G-kód psal ručně, tak půjdu touto cestou. Myslím si, že do

budoucí praxe mi tento postup jedině pomůže, a hlavně urychlí celý projekt.

## 6.1 Inventor CAM

První nápad byl Inventor a jeho vlastní CAM. Přeci jenom mám modely vymodelované

právě v tomto programu a v hodinách v rámci zaměření CNC jsem se s tímto CAM

programem učil. Logicky jsem si vyvodil, že by to neměl být problém.

Po různých pokusech jsem došel k závěru, že tento CAM je až moc silný nástroj na

domácí CNC frézku. Má neuvěřitelné možnosti obrábění, které jsou v mém případě

zbytečně složité. Proto jsem začal hledat další CAM.

## 6.2 Lazycam

Jako hlavní SW k frézce používám Mach3. Od firmy Artsoft existuje Lazycam, který je

prezentován právě k Mach3. Jeho hlavní výhoda je jednoduchost, protože vychází

z univerzálních DXF souborů. V tomto programu je možné zadat výkres a přiřadit výšku

polotovaru. Tím se vše zjednodušuje.

Věřím, že mezi sebou pracují dobře, jenže jsem se nedokázal dostatečně rychle

zorientovat v ovládání tohoto programu. Proto jsem zkusil mé štěstí a hledal další možný

CAM s nulovými náklady.

## 6.3 Estlcam 11

Tento CAM jsem našel v seznamu free frézovacích CAM programů. Prostředí z fotek

vypadlo natolik jednoduché, že jsem to nemohl tuto možnost nevyzkoušet. Stejně jako

Lazycam podporuje formát souborů DXF. Všechny parametry včetně řezných podmínek,

pohybů a samotného frézování se zadávaly jednoduše bez větších obtíží. Program je

velice jednoduchý a intuitivní.

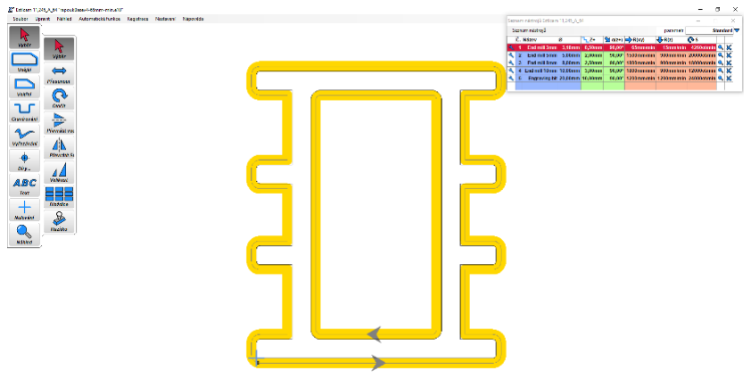
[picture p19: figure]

Obrázek 29 - Estlcam 11

Jediná jeho nevýhoda je počítadlo při spuštění. Dle napočítaného počítadla se zvedá čas

exportu, aby si uživatel musel koupit licencovanou verzi. Tento nedostatek kompletně

ignoruji, protože tento CAM je pro mé účely geniální. Proto tento program budu nadále

používat pro tvorbu G-kódů.

## 6.3.1 První frézování

Jako testovací materiál jsem si vybral to nejsložitější, co mohu obrábět, hliníkovou slitinu. Vše jsem chladil technickým lihem. Úspěšně jsem vyfrézoval první kapsu bez zlomení

nástroje. Samozřejmě jsem spočítal řezné podmínky, abych šanci tohoto neúspěchu

prakticky eliminoval (viz Příloha EE). Všechny výpočty jsem počítal v MS Excel. V této

situaci jsem nevěděl, co mě ještě čeká.

## 7 Chyby CNC frézky

Při každém vývoji se vždy objeví nějaké chyby, právě ty potkaly i mě.

## 7.1 Špatné rozměry

Když jsem vyfrézoval první kapsu v součásti, kterou jsem potřeboval na finální výrobek,

tak jsem nekontroloval rozměry. Počítal jsem s tím, že Mach3 frézku ovládá správně.

Po frézování vnější části konstrukce jsem narazil na tento problém. Křivky, které byly

naprogramovány, byly úplně jiné. Rozměry neodpovídaly a drážka nebyla ani rovná.

Nakonec stroj vyrobil kompletní nesmysl.

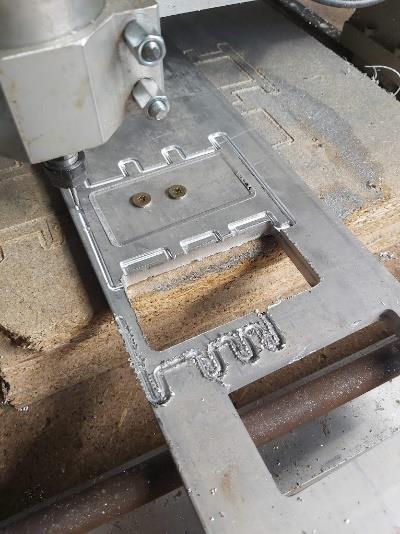
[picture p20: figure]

Obrázek 30 - Nepovedené obrábění na CNC

Problém mohl být jak v HW, tak i v SW. Ze začátku jsem nevěděl, čím by to mohlo být.

Proto jsem zkusil ten samý objekt vyfrézovat do dřeva. Výsledek byl perfektní. Tímto

jsem vyloučil problém ve stránce SW a začal hledat chybu ve frézce samotné.

Jako další test jsem chtěl vyfrézovat čtvercovou kostku o 10 mm. Výsledek místo těchto

rozměrů v ose X a Y byl rozdílný. Přesněji v ose X o 0,7 mm a v ose Y až o 1,5 mm.

Tento test mi ukázal, že krokové motory, nemají dostatečný výkon. Zmenšil jsem řeznou rychlost z 80 mm×min⁻¹

na 65 mm×min⁻¹
. Bohužel tato změna nijak tento problém

nevyřešila. Poslední, kde by mohl být problém jsou samotné motory.

## 7.2 Vylepšení motoru

Na ose Y jsem nechal přimontovaný původní krokový motor. Proto jsem použil stejný

pracovní postup jako při vylepšování motorů (viz Motory, strana 24). Dle výsledků z 10

mm kostky vidíme, že i osa X, která byla vylepšena, taktéž neodpovídá. Proto jsem na

řídící desce přidal maximální proud z 50 % na 100 %. Přestože se to může zdát jako velký

skok, tak jsem postupoval postupně. Při 100 % se krokové motory lehce zahřívaly. Lehké

zahřívání těmto motorům nijak nevadilo.

## 7.3 Nekolmá podložka

Při frézování jsem viděl, jak materiál zabírá do větší hloubky, když se pohybuje po ose

Y. To znamená, že obrobek není kolmo k vřetenu. Tento problém nemohu vyřešit. Mohl

bych vytvořit novou podložku, například stůl s drážkou ve tvaru “T”, avšak to by bylo

velmi časově i finančně náročné.

Jelikož jsem pracoval pouze ve 2,5D obrábění, tak jsem zvýšil nulový bod v ose Z. Tím

bych zmenšil hloubku záběru v první vrstvě. Ostatní vrstvy by se frézovaly stejně. Jiné

řešení jsem neměl.

## 7.4 Kontrola dotáhnutí šroubů

Jelikož nekontroluji, a ani neznám správné utahovací momenty, na které se mají stavěcí

šrouby dotahovat, tak občas se nějaký povolí. Toto se mi stalo uprostřed frézování kloubu.

Naštěstí se nástroj nezlomil. Pouze jsem přišel o kus materiálu.

## 7.5 Free verze Mach3

V průběhu frézování jsem zjistil, že free verze SW dokáže pracovat s G-kódy maximální

do 500 řádků. Nejdelší G-kód, který jsem naprogramoval, měl 1150 řádků. Z tohoto

důvodu jsem musel G-kódy rozdělovat podle pořadí operací. Musel jsem vymazat přebývající mezery a nepotřebné příkazy. Naštěstí se největší součást mohla vložit do

dvou G-kódů.

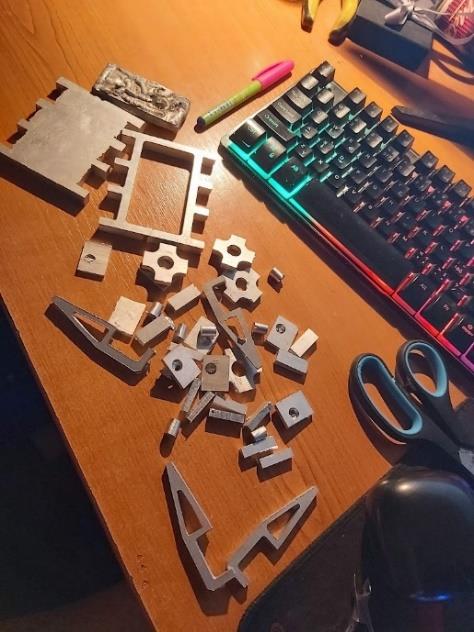
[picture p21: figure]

Obrázek 31 - Vyfrézované součásti

## 8 Sváření

Opět jsem chtěl tento projekt posunout o krok dál. Z tohoto důvodu jsem ustoupil od

klasického šroubového spoje, a vybral si sváření hliníku.

## 8.1 Problematika sváření hliníku

Problém není v samotném materiálu, ale v jeho oxidační vrstvě Al2O3. Ta má teplotu

tavení okolo 2000 °C, přičemž samotný hliník má 660,3 °C. Při zahřátí čistého hliníku na

teplotu, při které se oxid hliníku taví, by se okamžitě vypařil. Proto využíváme střídavého

napětí (viz Nastavení svářečky, strana 37), který nám TIG nabízí. Též je možné použít

MIG se střídavým napětím a další technologie, ale těch jsem nevyužil.

## 8.2 Metoda TIG

U hliníku není tolik možností sváření jako u oceli, ale stále nějaké existují. Vybral jsem

si nejrozšířenější metodu TIG. Zkratka TIG znamená Tungsten inert gas. Jedná se o

elektrodu v inertním plynu, kterým je argon. Při sváření ocelí se může kombinovat s CO2.

U hliníku musí být vždy vše čisté. Proto se používá plyn s obsahem 99 % argonu neboli

téměř čistý argon.

## 8.3 Moje vybavení

Používám svářečku TIG200PAC/DC od firmy Jasic. Jedná se o analogovou svářečku,

která místo displeje používá potenciometry. Díky vetší velikosti zvládne vyšší zátěž. Též

má vyšší frekvenci. Je možnost svářečku přepnout do metody MMA.

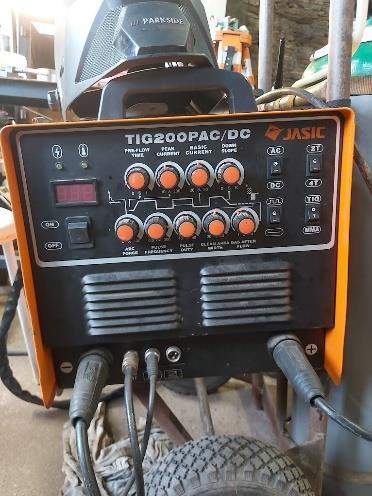
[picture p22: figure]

Obrázek 32 - TIG svářečka

## 8.4 Nastavení svářečky

Zde popisuji každé nastavení, se kterým jsem se setkal. Používal jsem dvoutaktní sváření.

Během svařování je tlačítko stisknuté, dokud nedokončíme svar.

## 8.4.1 DC/AC a čistění

Metoda TIG nám umožňuje sváření se střídavým (AC) a stejnosměrným (DC) napětím,

které dále může být s pulzem nebo bez pulzu. U hliníku jsem využil AC napětí, ale viděl

jsem i nastavení na DC s pulzem. Dále je důležité čištění, jinak označeno jako AC

Balance. Tento údaj udává, v jakém poměru bude kladný pól se záporným. Přesně toto

zajistí poškození oxidační vrstvy a svařuje jádro materiálu dohromady. (15) (viz

Problematika sváření hliníku, strana 36). Většinou se používá 20-30 % intervalu na

kladném pólu elektrody. Svařil jsem s nastavením 50/50. Nedokázal jsem moc poznat

rozdíl. Z toho důvodu mi nastavení 50/50 připadalo jako nejlepší.

## 8.4.2 Frekvence

Další z pojmů, se kterými jsem se setkal, byla frekvence. Ze samotného názvu lez

odvodit, jakou funkci bude zastupovat. Jedná se o počet opakování střídání polarity napětí. Udává se v jednotce 1 Hz. Pro pochopení lze frekvenci přirovnat k nástrojům.

„Vysoká frekvence je jako skalpel, nízká jako kladivo“. (15) Přesně tohoto přirovnání

jsem se držel a doopravdy to takto funguje. Pokud budu svařovat hliníkové plechovky,

použiji vysokou frekvenci. Když budu svářet široký materiál (nad 5 mm), použiji nižší

okolo 60 Hz. Zajímavost je ta, že rozdílná frekvence lze i slyšet.

Rozsah na mé svářečce je 0-300 Hz. Profesionálové používají svářečky, které mají

maximální frekvenci 250 Hz. To opět ukazuje na vysokou kvalitu vybavení, které jsem

měl k dispozici.

## 8.4.3 Proudy

U sváření se nastavuje maximální proud. Čím vyšší proud, tím více dodáváme tepla do

svařence. Začínal jsem na 120 A, kdy jsem postupně snižoval až na 55 A.

Jsou zde dvě nastavení. Základní a maximální proud. Základní je proud, který bude na

začátku svaru. Následně se svářečka řídí podle základního proudu, dokud nepřestaneme

svářet. I toto je důležité pro správný průnik skrz oxidovou vrstvu.

## 8.4.4 Zapojení pólu svářečky

U metody TIG je toto přesně naopak. Většinou kostra je na záporném pólu svářečky a

svářecí pistole na kladném. Toto je zde přesně naopak. Zkoušel jsem standartní zapojení,

bohužel se mi začala tavit elektroda.

## 8.4.5 Ostatní nastavení

Nesmíme zapomenout na doběh proudu. Při vypnutí svařování se proud postupně snižuje.

Díky tomuto opatření nevznikají krátery na konci svaru, které svar zeslabují. Nastavuje

se časově. Většinou se tato hodnota nastaví mezi 3 až 5 sekundami.

Dofukování/ochlazování po svařování nám ochlazuje elektrodu. To eliminuje oxidaci

samotné elektrody, když je ve vysokých teplotách.

## 8.5 Elektrody

Elektrod k metodě TIG je nespočet. Především se rozdělují na AC, DC napětí a

univerzální. Následně dle materiálu. Jsou rozděleny dle barev, kdy zelená je určená pro

hliník.

Ze začátku jsem použil používanou elektrodu a natolik poškrabanou, že jsem nedokázal

rozeznat její určení. Myslel jsem si, že je univerzální, jenže původně byla červená. Ta se

používá na ocel. Ve spojení se špatným nastavením svářečky a neočištěným materiálem

mi hliník nešel svařit. Avšak po splnění všech těchto bodů jsem úspěšně začal svářet.

Obrázek 33 - Wolframové elektrod (16)

## 8.6 Čistota a výběr materiálu

Jak jsem zmínil v předchozích bodech, hliník potřebuje vysokou čistotu. Pokud se i

drobná nečistota dostane do svaru, dojde k vysoké oxidaci. Největší problém je

v nečistotách svařovací pistole. Mnoho začátečníků tuto podmínku přehlíží. Po mnoha

hodinách svařování jsem nevyčistil pistoli ani jednou. Následně se mi vše vrátilo a mohl

jsem svařovanou součást přidat do sbírky nepovedených svařenců. Když se mi do svaru

dostalo velké množství nečistot, tak jsem nebyl schopen svar ani ohřát.

S přibývající teplotou se ohřívá i okolní materiál, který se následně roztaví. Jakmile se

tento jev stane, tak není jiná možnost než odstranit nečistoty nebo svařit další součást z

nových kusů materiálu. Na odstranění nečistot jsem používal pilník nebo brusný papír,

ale i tato metoda není 100% úspěšná.

Existuje nespočet různých druhů slitin přídavného materiálu, přičemž jsem používal

pouze AlSi5. Zmíněný přídavný materiál je nejuniverzálnější. Tuto informaci jsem dostal

od prodejce svařovací techniky.

## 8.7 Moje zkušenosti se svařováním hliníku a metody

## TIG

Chtěl bych zde zdůraznit, že se rozhodně nejedná o profesionální svařování. Nemám

svářečské zkoušky (svářel jsem pouze pod dohledem způsobilé osoby) a učím se

především z internetu. Před začátkem této práce jsem s metodou TIG pracoval asi třikrát.

Přičemž jsem především zkoušel nerezovou ocel. Hliník jsem si poprvé zkusil až v této práci. Z toho důvodu některé svary nevypadají, jak by měly správně vypadat. O těchto

nedostatcích vím. Věřím, že s přibývající praxí se bude moje svařovací technika

zlepšovat.

## 8.8 Postup čištění a příprava na svařování

Nechtěl jsem nic podcenit, a proto jsem po vyčištění pistole postupoval dalším čištěním.

## 8.8.1 Chemické čištění

Svařované součásti jsem čistil acetonem. Ze začátku jsem je čistil isopropylalkoholem.

Avšak po zkoušení a doporučení jsem zjistil, že aceton je lepší.

Obrázek 34 - Nečistoty z čištění

## 8.8.2 Mechanické čištění

Na mechanické čistění jsem použil drátěný kartáč. Následně i brusný papír o hrubosti

240. Jednoduše jsem doopravdy nechtěl nic podcenit.

Ještě jednou jsem otřel celý povrch látkou nebo vatovým polštářkem napuštěnou

acetonem.

Obrázek 35 - Součásti po vybroušení

## 8.8.3 Předehřívání

Hliník se může před svářením předehřát okolo 200 °C. To nám zajistí lepší svařovatelnost

hliníku. Tento postup jsem vyzkoušel, přestože jsem nesvařoval natolik objemné součásti,

aby tento postup byl potřeba. Elektrický oblouk ohřál svařované součásti velice rychle.

## 8.9 Potřebná ochrana

Jako před každým svářením se musí svářeč dostatečně chránit. Svařovací kukla je základ,

stejně jako rukavice, oblečení a kožené boty. U hliníku je navíc potřeba odvětrávaná

kukla, která stojí nemalé peníze. Jelikož tuto kuklu jsem neměl k dispozici, tak jsem

použil respirátor FFP2. Bez ochrany dýchacích cest jsem se okamžitě začal dusit.

Kdybych věděl, kolik hodin strávím čistým svářením, tak bych použil dýchací masku od

3M. Každopádně respirátor fungoval a masku bych použil pouze pro zlepšení komfortu.

## 8.10 Kontrola svaru

Na mém pracovišti nemám k dispozici žádnou nedestruktivní metodu kontroly svaru.

Proto mi pouze zbývala destruktivní hrubá síla mých rukou. U každého svaru jsem použil

pár kombinovaných kleští a vyzkoušel, zda svar je dostatečně pevný především na ohyb

a krut. Svary, které jsem dělal jako první, praskly téměř okamžitě. Materiál jsem

dostatečně neprohřál a následně hodně obrousil. Po tomto zjištění jsem opět součásti

očistil a svařil znovu a lépe. Následná kontrola dopadla dobře.

Obrázek 36 – Kontrola svaru pomocí zraku

## 9 Tvorba závitů

Vybral jsem šroubové spoje s vnitřní šestihrannou hlavou o průměru závitu 2 mm. Šrouby

jsem koupil na čínském webu v sadě s různými délkami těla šroubu. Jedná se o metrické

šrouby se standartním stoupáním 0,4 mm.

Díry jsem si označil automatickým důlkovačem a předvrtal vrtákem o průměru 1 mm na stojanové vrtačce. Řezné podmínky jsem nebral v potaz. Na chlazení jsem použil

technický líh.

Dle následujícího výpočtu jsem použil vrták o průměru:

Průměr závitu × 0,8 = Průměr díry

2 × 0,8 = 1,6 mm

Rovnice 2 - Výpočet průměru vrtáku

Samozřejmě pokud bych si tento výpočet nepamatoval, anebo jsem o tomto výpočtu

nevěděl, hledal bych ve strojnických tabulkách.

Dále jsem postupoval vyříznutím závitu pomocí strojního závitníku do děr, který jsem

koupil na webu eshop.nastrojecz.cz. K závitníku jsem přikoupil olej na vyřezávání závitů

do hliníku a jeho slitin. Hlavní rozdíl oproti standartnímu řeznému oleji byl v hustotě.

Závity jsem ručně vyřízl pomocí vratidla. Zaoblil hrany pomocí kuželového záhlubníku

a vytvořený závit odzkoušel.

## 10 Komponenty a realizace pavouka

## 10.1 Servomotory

Na začátku projektu jsem počítal se servomotory s převodem z nylonu. Jakmile jsem

použil kokovou konstrukci, tak jsem musel použít i převod z kovu v servomotorech.

Přestože výpočtově bych mohl použít nylonové převody (viz Výpočty, strana 11), tak mi

nepřijde logické mít kovovou konstrukci a kombinovat ji s plastovými převody. Místo

servomotoru SG90 9 g jsem použil EMAX ES08MA II 12 g.

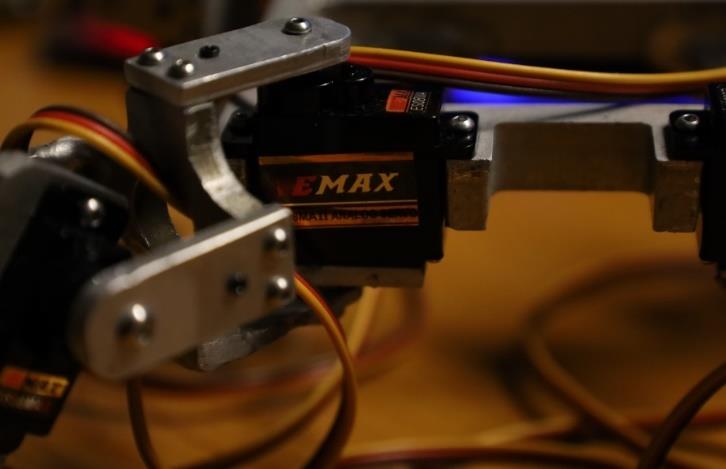
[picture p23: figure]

Obrázek 37 - Servomotor EMAX ES08MA II

## 10.2 Základní deska

Pro testování pohybu používám klon Arduino UNO. Ve finálním provedení počítám

s ESP8266 Amica nebo Lua. Obě desky podporují komunikaci pomocí Wi-Fi, kterou

v tomto projektu potřebuji.

## 10.3 Realizace

Po dokončení všech potřebných úprav vyfrézovaných součástí jsem začal konstrukci

skládat dohromady. Nejdříve jsem začal se základním rámem a připojení servomotoru

(viz Obrázek 38 - Základní rám). Následně jsem přišrouboval servomotory k nohám a vše

spojil klouby.

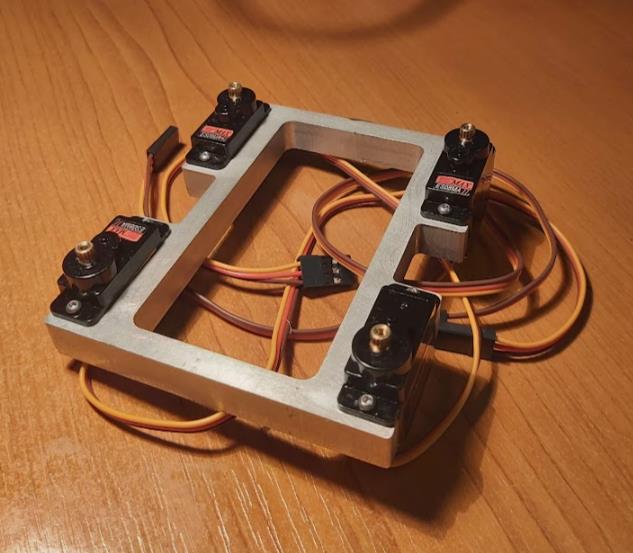
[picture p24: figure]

Obrázek 38 - Základní rám

Po složení jsem si všiml velkých vůlí v uložení servomotorů. Proto do kloubu, ve kterém

držela i páka servomotoru, jsem vyvrtal díry. Jedním šroubem jsem spojil osu

servomotoru s konstrukcí. Druhým vrutem, o průměru 1 mm, jsem zajistil nepřesnosti

otvoru pro páku (viz Příloha N).

Tímto opatřením jsem vymezil všechny vůle a stále jsem udržel rozebíratelnost robota.

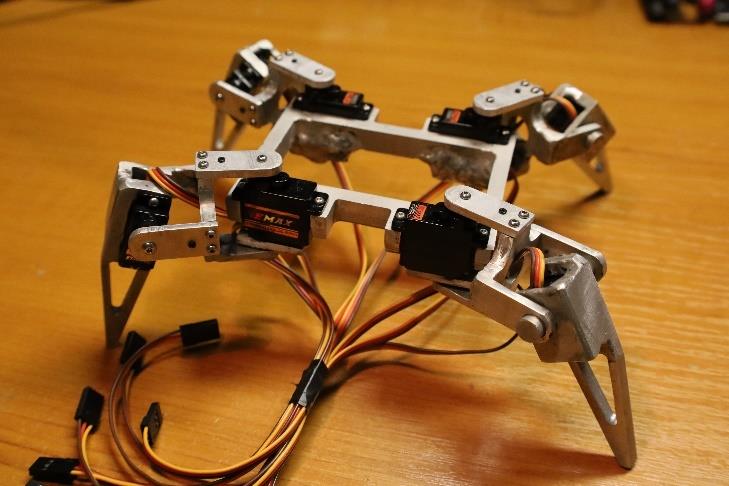
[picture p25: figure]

Obrázek 39 - Finální konstrukce pavouka

## 11 Tvorba technické dokumentace

## 11.1 Sestava

Sestavy mě fascinovaly už od útlého věku, kdy jsem viděl různé animace skládajících se

částí. Před touto ročníkovou prací jsem neměl tušení, jak se se sestavami pracuje. Během

výuky jsem se naučil celý průběh sestavy a využívání správných funkcí (viz Příloha A).

Na internetu jsem našel model servomotoru, který používám na pavoukovi. Z důvodu

časové náročnosti jsem zvolil použít tento model. Model byl vyexportován ve formátu

SLDPRT (SolidWorks part) (17)

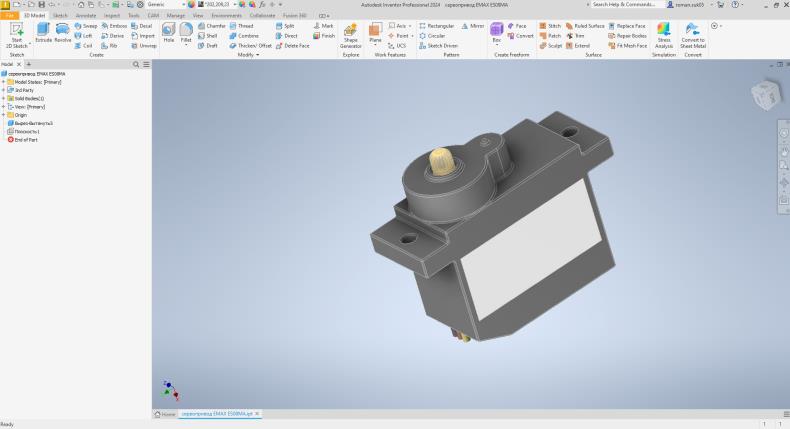
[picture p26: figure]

Obrázek 40 - Model servomotoru

## 11.2 Proč jsem si vybral bezvýkresovou dokumentaci

Ze začátku jsem počítal s klasickou výkresovou dokumentací. V průběhu třetího ročníku

jsem objevil bezvýkresovou dokumentaci, kterou mi ukázal můj vedoucí práce. Byla to pro mě kompletně nová věc. Z logiky věci mi přišla tato metoda technické dokumentace

rychlejší a jednodušší. Jelikož cíl této práce bylo si vyzkoušet mé schopnosti a dobře se

naučit nové věci, tak jsem okamžitě začal pracovat na bezvýkresové dokumentaci.

## 11.3 Princip bezvýkresové dokumentace

V bezvýkresové dokumentaci nemusíme vytvářet výkres, protože všechny důležité

informace a kóty zapíšeme do modelu, který potřebujeme vyrobit.

Výhoda této metody je v jednoduchosti a uspořádání souborů. Není potřeba párovat

k sobě dva dokumenty a držet je při sobě, protože vše je obsaženo v jednom dokumentu.

Samozřejmě je zde i jedna veliká nevýhoda. Bezvýkresová dokumentace se obtížně tiskne

– je určena na 3D prohlížení v PC.

Jelikož se snažím nejvíce využívat i ostatní jazyky, tak všechen software, který jsem

potřeboval k tvorbě technické dokumentace, mám nastavený v anglickém jazyce. Proto

kóty jsou v anglickém jazyce.

## 12 Závěr

Naplnění zadání tématu bylo splněno. Na začátku projektu jsem si myslel, že práce

nebude tak časově náročná. Můj časový odhad byl okolo 80 hodin práce. Odhad nebyl

nejpřesnější, protože projekt byl téměř 3krát delší (viz Příloha EE). Než jsem vytvořil

základní konstrukci pavouka, která byla plně funkční, a splnil další nutné operace, zabralo

mi to hodně času. Pouze sváření jsem se nezvládl naučit na 100 %. Největší problém u

sváření je, že je potřeba mnoho času a zkušeností. Bohužel ani 40 hodin, strávených

svářením, mi nestačilo na vizuálně perfektní svary. Naopak svary jsou pevné, nepraskají

a nelámou se.

Osobním cílem především bylo odzkoušet a rozšířit si zkušenosti v oblasti robotiky a

CNC strojů. Jednoznačně mohu potvrdit, že ke zlepšení došlo. Též jsem pochopil účel

sestavy. Během modelování jsem udělal chybu z důvodu špatného měření, ale kdybych

si celou sestavu udělal před frézováním, tak bych ji objevil dříve. Tento poznatek je

největším přínosem této práce. Pokud bych tuto práci vypracovával znovu, tak bych si

zvolil větší přídavky na obrábění, abych mohl finální konstrukci lépe vybrousit.

Pavouk funguje na jednoduchých čtyřech nohách z hliníkové slitiny, které jsou osazeny

servomotory EMAX ES08MA II. Každá noha disponuje dvěma těmito servomotory,

s jejichž pomocí a rychlou dynamikou se dokáže pohybovat do všech směrů. Tělo se hýbe

po jakési „hranaté sinusoidě“, tím pádem se tělo mého pavouka nikdy nebude pohybovat

ve stejné výšce. V této části práce jsem se zaobíral výrobou konstrukce na vlastní CNC

frézce a v druhé části budu vytvářet software a motherboard.

Závěrem bych chtěl doplnit, že nezáleží na obtížnosti projektu, nýbrž na faktoru zábavy,

který mi pomohl zvládnout toto téma a vypracovat jej bez zbytečné prokrastinace.

## 13 Seznam použité literatury

1. DFROBOTCN. SpiderBot！This is TOO CUTE lol. Youtube. [Online] 5. Listopad

2019. [Citace: 2. Únor 2024.] https://www.youtube.com/shorts/3u1M04DwSdE.

2. DIY Builder. How To Make A Spider Robot. YouTube. [Online] 30. Leden 2020. [Citace: 2. Únor 2024.] https://www.youtube.com/watch?v=8LSOoVZbfFM.
3. Zaxtruder. Autonomous 3D Printed QuadSpider Robot. YouTube. [Online] 18. Červen

2020. [Citace: 2. Únor 2024.] https://www.youtube.com/watch?v=04VkpGuIz30.

4. Maker 101. How to make Quadruped Spider Robot (using Arduino and 3D parts).
YouTube. | [Online] | 31. | Říjen | 2022. | [Citace: | 2. | Únor | 2024.]

https://www.youtube.com/watch?v=sDuzb-I00-4.

5. STEM Education. Spider robot with Arduino DIY ,wifi robot running test. YouTube.
[Online] | 12. | Červenec | 2020. | [Citace: | 2. | Únor | 2024.]

https://www.youtube.com/watch?v=YmWVJWwuqLI.

6. Ullis Roboter Seite. SG90 9 g Micro Sevo. Ullis Roboter Seite. [Online] [Citace: 2.
Únor | 2024.] | https://ullisroboterseite.de/projekte-

teedipper/SG90%209%20g%20Micro%20Servo.pdf.

7. Tech Plasty. PA6 - extrudovaný polyamid. Tech Plasty. [Online] [Citace: 2. Únor

2024.] https://www.techplasty.cz/material/polyamid/pa6-extrudovany-polyamid.

8. IMC Slovakia s.r.o. Vlastnosti a normy hliníkových zliatín. hlinik.sk. [Online] [Citace:
2. Únor 2024.] https://www.hlinik.sk/vlastnosti-a-normy-hlinikovych-zliatin/.
9. Reprap přispěvatelé. 4 Axis TB6560 CNC Stepper Motor Driver Board Controller.
Reprap. | [Online] | 29. | Listopad | 2014. | [Citace: | 2. | Únor | 2024.]

https://reprap.org/wiki/4_Axis_TB6560_CNC_Stepper_Motor_Driver_Board_Controlle

r.

10. Beekeeper. 12 Volt Power Supply Cover. Thingiverse. [Online] 5. Leden 2013. [Citace: 2. Únor 2024.] https://www.thingiverse.com/thing:40377.
11. ARTSOFT STUDIOS. Mach3. MachSupport. [Online] [Citace: 2. Únor 2024.]

https://www.machsupport.com/shop/mach3/.

12. PavelZ. Uživatelská příručka pro instalaci, konfiguraci a používání Mach3. cnc1.
[Online] | Listopad | | 2008. | [Citace: | 2. | | Únor | 2024.]

http://www.cnc1.eu/files/images/stories/mach3/Mach3Mill_CZ.pdf.

13. Build Your CNC. Question #: 554. Build Your CNC. [Online] [Citace: 2. Únor 2024.]

https://buildyourcnc.com/FAQ/554.

14. Yosquad. Konfiguracja mach3 motor tuning. cnc.onfo.pl. [Online] 16. Červen 2016.

[Citace: 2. Únor 2024.] https://www.cnc.info.pl/konfiguracja-mach3-motor-tuning-

t77610.html.

15. Solík SK, s.r.o. Ako zvárať hliník - nastavenie parametrov zváračky na hliník.
YouTube. | [Online] | 25. | Září | 2020. | [Citace: | 2. | Únor | 2024.]

https://www.youtube.com/watch?v=d9h5MNtsRcs.

16. Svářecí kukla. Wolframové elektrody. Svářecí kukla. [Online] [Citace: 2. Únor

2024.] https://www.svarecikukla.cz/wolframove-elektrody/.

17. Alexandr Poluyan. Servo EMAX ES08MA. GrabCAD. [Online] 1. Prosinec 2023. [Citace: 2. Únor 2024.] https://grabcad.com/library/servo-emax-es08ma-1.

## 14 Seznam grafických objektů

## 15 Seznam tabulek

## 16 Seznam rovnic

## 17 Seznam zkratek

Zkratka | Původní slovo | Význam
RC | Remote control | Dálkové ovládání
MS | Microsoft | Název
MS-DOS | Microsoft – Disk Operating System | Microsoft – Diskový Operační Systém
DOS | Disk Operating System | Diskový Operační Systém
S4 | Step-four | Název
SW | Software | Program
HW | Hardware | Fyzické komponenty výpočetní techniky
CAM | Computer aided manufacturing | Výroba podporovaná počítačem
CNC | Computer Numerical Control | Výpočtové ovládání pomocí počítače

## 18 Seznam příloh

### 18.1 Technická dokumentace

Příloha A | rapoukAssemblyv2.iam
Příloha B | rapoukBaseAssemblyv1.iam
Příloha C | rapoukLegAssemblyv0.iam
Příloha D | rapoukMiddleLegAssemblyv0.iam
Příloha E | rapoukBasev5.ipt
Příloha F | rapoukLegBasev3.ipt
Příloha G | rapoukLegPinv1.ipt
Příloha H | rapoukLegSupportv1.ipt
Příloha I | rapoukLegSupportv2.ipt
Příloha J | rapoukLegv9.ipt
Příloha K | rapoukMiddleLeg0v3.ipt
Příloha L | rapoukMiddleLeg1v3.ipt
Příloha M | rapoukMiddleLeg2v3.ipt
Příloha N | rapoukServoLegv0.ipt
Příloha O | rapoukHexagonScrewM2,5v0.ipt
Příloha P | rapoukHexagonScrewM2v0.ipt
Příloha Q | сервопривод EMAX ES08MA.ipt
Příloha R | сервопривод EMAX ES08MA.SLDPRT

### 18.2 G-kódy

Příloha S | rapoukBasev5
Příloha T | rapoukLegBasev3
Příloha U | rapoukLegPinv1
Příloha V | rapoukLegSupport5mm
Příloha W | rapoukLegSupport10mm
Příloha X | rapoukLegv9X
Příloha Y | rapoukLegv9Y
Příloha Z | rapoukMiddleLeg0v3

Příloha AA rapoukMiddleLeg1v3

Příloha BB rapoukMiddleLeg2v3

### 18.3 Textové soubory a vizualizace

Příloha CC Rapouk.docx

Příloha DD Rapouk.pdf

Příloha EE Rapouk.xlsx

Příloha FF IMG_0446.jpg

Příloha GG IMG_0458.jpg

Příloha HH Vizualizace.png



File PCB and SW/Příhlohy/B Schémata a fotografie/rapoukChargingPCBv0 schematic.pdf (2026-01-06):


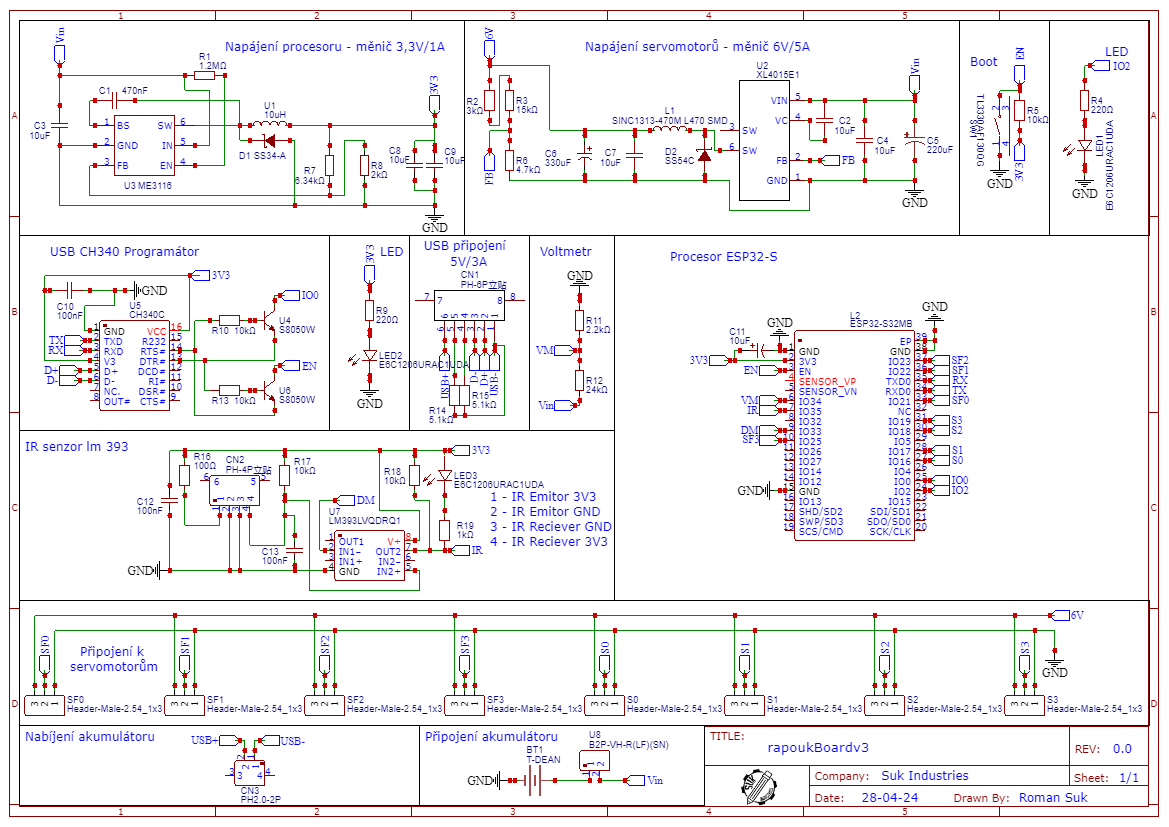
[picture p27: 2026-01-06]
easyEDA/screenshot/Schematic_rapoukBoardv6_2024-06-18.png

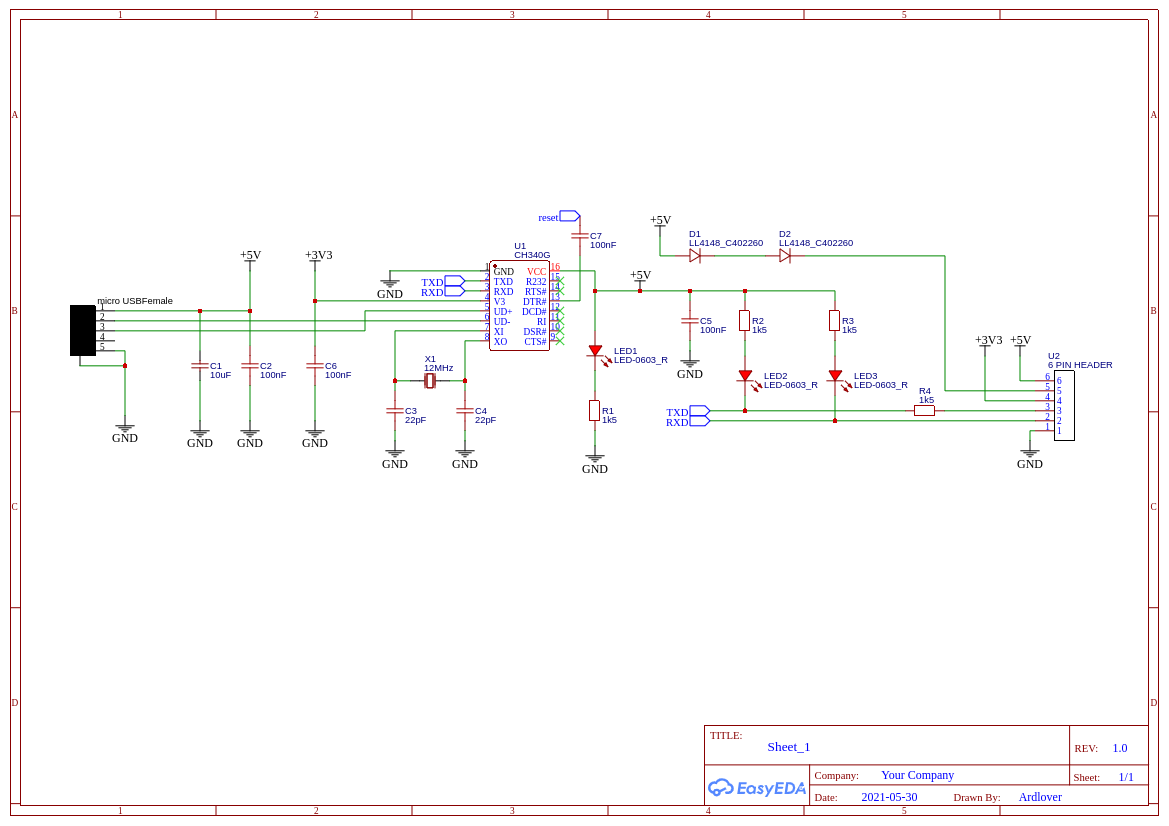
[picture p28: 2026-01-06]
Datasheet and pics/Schematic_ch340g usb to ttl_2021-07-28.png

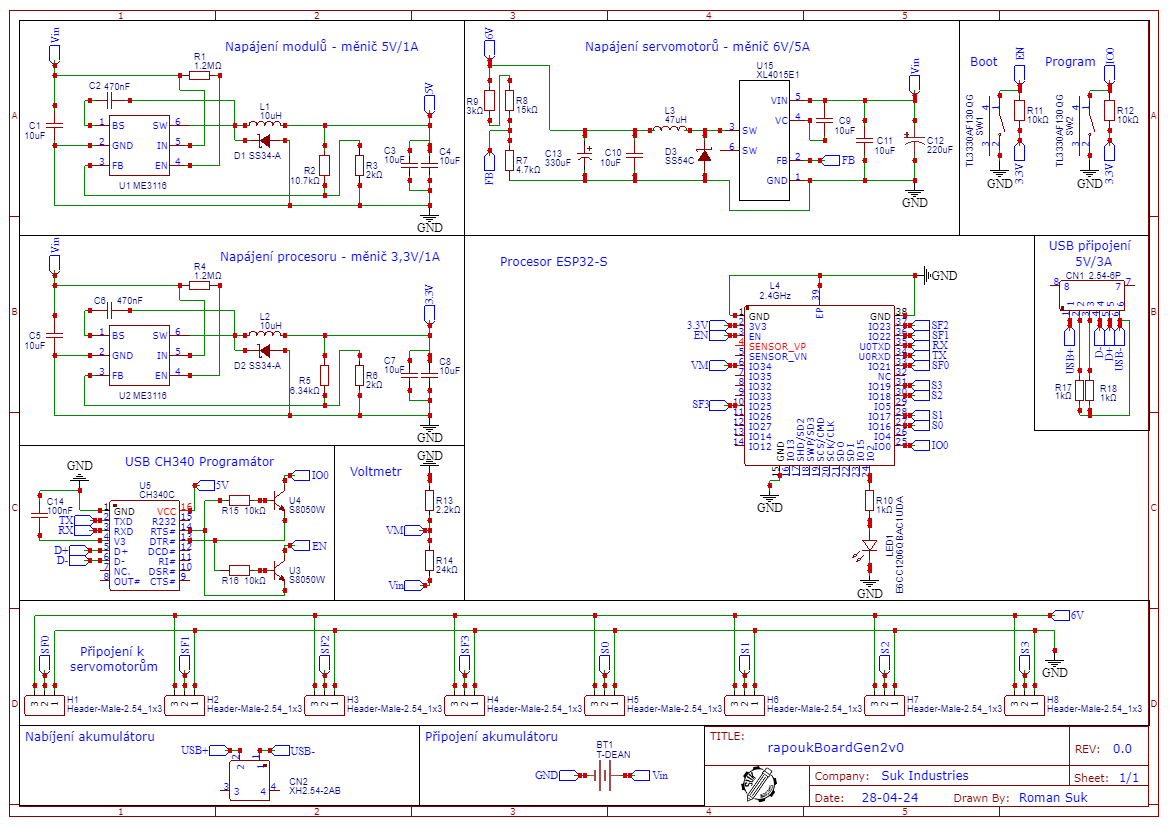
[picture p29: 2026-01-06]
easyEDA/projects/Měnič2/Schematic_Měnič2_2024-04-28.png

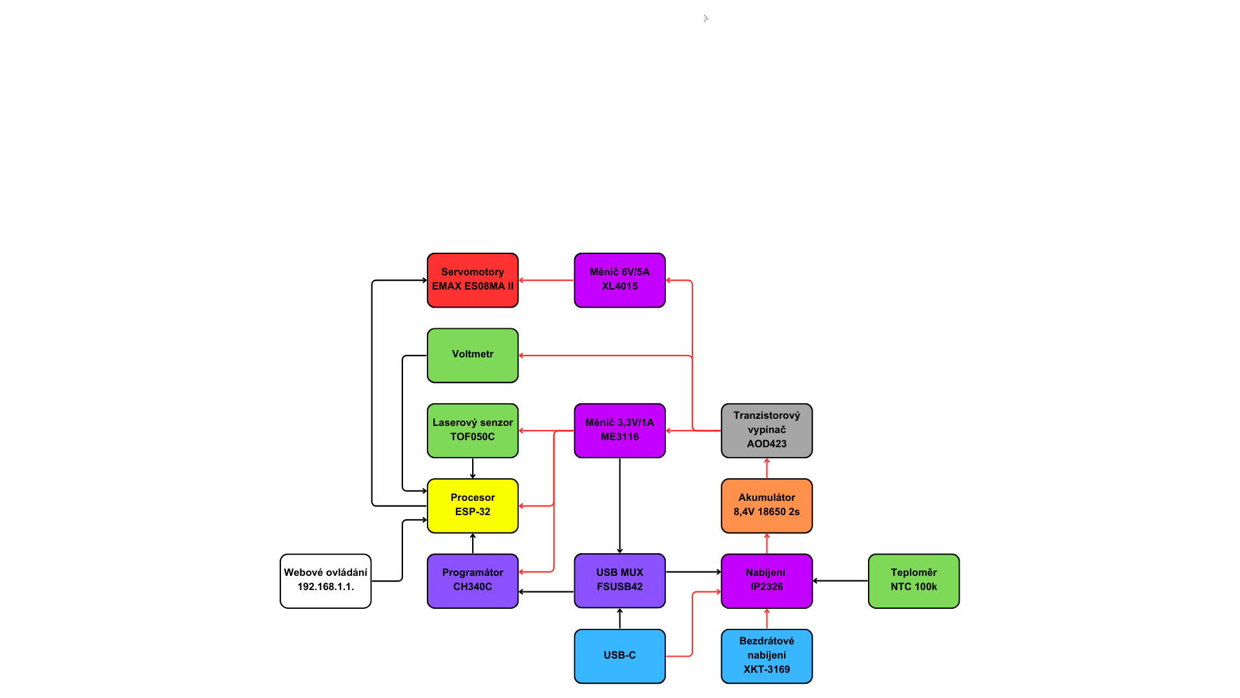
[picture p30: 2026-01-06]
blockDiagram.png

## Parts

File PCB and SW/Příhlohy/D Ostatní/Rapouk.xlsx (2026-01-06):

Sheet: Čas
Čas projektu
Teoretická/PC část |  |  | Praktická část
Zadání | Čas (h) | Datum | Zadání | Čas (h) | Datum
Návrh baterie a komponentů | 2.00 | 2023-03-24 | Tisk | 0.75 | 2023-06-15
Počítání napětí (ohyb) | 2.50 | 2023-03-30 | Tisk | 0.75 | 2023-06-16
Schéma | 0.50 | 2023-03-05 | Testování modelů | 2.50 | 2023-06-17
Eagle | 2.00 | 2023-04-07 | Tisk | 2.50 | 2023-06-17
Skládání | 2.00 | 2023-04-10 | Tisk | 1.50 | 2023-06-18
SW | 1.20 | 2023-04-29 | Tisk | 0.20 | 2023-06-25
SW | 2.00 | 2023-04-12 | Příprava a hledání materiálu | 0.50 | 2023-07-22
SW | 2.00 | 2023-05-07 | Tvorba základu | 2.00 | 2023-07-22
SW | 3.00 | 2023-05-15 | Příprava CNC frézy | 1.00 | 2023-07-22
SW | 1.50 | 2023-05-27 | Zkouška DOSu | 2.00 | 2023-07-23
Modelování | 3.00 | 2023-05-29 | Tisk spojky | 0.25 | 2023-07-23
Modelování | 1.00 | 2023-06-15 | Zkouška DOSu | 1.50 | 2023-07-24
Modelování | 1.00 | 2023-06-16 | Oprava motorů na CNC | 1.00 | 2023-07-25
Modelování základu | 0.75 | 2023-06-17 | Čištění | 1.00 | 2023-07-26
Modelování | 1.00 | 2023-06-17 | Čištění | 1.00 | 2023-07-27
Modelování | 0.50 | 2023-06-18 | První zkouška | 1.00 | 2023-07-27
Modelování | 1.50 | 2023-06-22 | Řešení chyb | 1.50 | 2023-07-30
Modelování | 3.00 | 2023-06-25 | Zkouška zákl. desek a nastavení | 2.00 | 2023-07-31
Tvorba spojky | 0.25 | 2023-07-23 | Rozpohybování os | 4.00 | 2023-07-31
Nastavování Mach3 | 1.00 | 2023-08-02 | Sestavání sestavy PC | 4.00 | 2023-08-05
Nastavování Mach3 | 1.00 | 2023-08-04 | Vylepšení | 1.00 | 2023-08-12
Instalace DOSu | 6.00 | 2023-08-06 | Tvorba spojky | 3.00 | 2023-08-18
Instalace DOSu + komponenty | 5.00 | 2023-08-07 | Promazávání a zkoušky | 0.75 | 2023-09-04
Modelování | 1.00 | 2023-10-12 | Kabeláž k vřetenu | 0.50 | 2023-09-05
Tvorba schéma | 1.00 | 2023-11-12 | Předělávání vozíku | 1.50 | 2023-09-11
Tvorba schéma | 1.00 | 2023-11-12 | Tisk krytky na zdroj | 0.50 | 2023-09-11
Tvorba schéma | 3.50 | 2023-11-13 | Zkompletování | 0.50 | 2023-09-12
Tvorba schéma | 2.00 | 2023-11-15 | Příprava na frézování | 2.00 | 2023-09-13
Modelování přípravku | 0.75 | 2023-12-03 | První frézování | 2.00 | 2023-09-18
Tvorba schéma | 1.50 | 2023-12-04 | Frézování | 6.00 | 2023-09-23
Převod schéma do PC | 1.50 | 2023-12-05 | Ladění chyb | 3.00 | 2023-09-24
Technická dokumentace | 0.75 | 2024-01-02 | Frézování | 6.00 | 2023-09-30
Sestava | 1.00 | 2024-01-09 | Frézování | 4.50 | 2023-10-02
Sary v tech. doku. | 1.50 | 2024-01-23 | Náuka svařování | 0.50 | 2023-10-01
Sestava | 3.50 | 2024-01-30 | Náuka svařování | 0.50 | 2023-10-02
Sestava | 4.50 | 2024-02-03 | Náuka svařování | 1.00 | 2023-10-03
Sestava | 1.00 | 2024-02-04 | Frézování | 4.50 | 2023-10-08
Sestava a TTD | 6.75 | 2024-02-06 | Frézování | 3.00 | 2023-10-09
Tvorba videa | 1.00 | 2024-02-06 | Frézování | 4.25 | 2023-10-15
Sestava | 1.25 | 2024-02-07 | Frézování | 1.00 | 2023-10-16
Sestava | 0.75 | 2024-02-08 | Frézování | 0.75 | 2023-10-19
TTD | 2.00 | 2024-02-09 | Ladění chyb/frézování | 4.50 | 2023-10-22
TTD | 2.25 | 2024-02-13 | Čistění | 3.00 | 2023-10-25
Tvorba videa | 1.50 | 2024-02-26 | Frézování | 7.00 | 2023-10-26
Tvorba schéma | 0.75 | 2024-02-27 | Frézování | 1.25 | 2023-10-27
Tvorba schéma | 3.50 | 2024-02-28 | Frézování | 5.50 | 2023-10-28
Tvorba schéma | 4.75 | 2024-03-03 | Frézování | 4.00 | 2023-10-29
Tvorba schéma | 1.00 | 2024-03-04 | Zaoblení hran | 0.75 | 2023-11-09
Skládání a testování | 2.50 | 2024-03-07 | Zaoblení hran | 0.50 | 2023-11-10
Příprava na prezentaci | 3.00 | 2024-03-10 | Zaoblení hran | 0.50 | 2023-10-11
 |  |  | Zaoblení hran | 0.50 | 2023-10-12
 |  |  | Stůl na sváření | 1.00 | 2023-11-17
 |  |  | Náuka svařování | 4.50 | 2023-11-18
 |  |  | Svařování | 1.00 | 2023-11-19
 |  |  | Svařování | 2.50 | 2023-11-21
 |  |  | Svařování | 3.00 | 2023-11-22
 |  |  | Svařování | 1.00 | 2023-11-24
 |  |  | Svařování a broušení | 2.00 | 2023-11-25
 |  |  | Svařování a broušení | 4.00 | 2023-11-26
 |  |  | Svařování | 1.00 | 2023-11-27
 |  |  | Svařování | 1.75 | 2023-11-28
 |  |  | Svařování a broušení | 1.50 | 2023-11-29
 |  |  | Svařování | 1.50 | 2023-11-30
 |  |  | Svařování | 1.50 | 2023-12-01
 |  |  | Tisk | 0.30 | 2023-12-03
 |  |  | Vrtání a tvorba závitů | 2.50 | 2023-12-03
 |  |  | Testování schéma | 2.50 | 2023-12-06
 |  |  | Testování schéma | 4.00 | 2023-12-07
 |  |  | Testování schéma | 6.00 | 2023-12-08
 |  |  | Testování schéma | 4.00 | 2023-12-09
 |  |  | Svařování a broušení | 2.00 | 2023-12-09
 |  |  | Svařování a broušení | 2.25 | 2023-12-10
 |  |  | Frézování | 2.25 | 2023-12-11
 |  |  | Testování schéma | 1.25 | 2023-12-11
 |  |  | Svařování a broušení | 2.50 | 2023-12-13
 |  |  | Svařování | 1.00 | 2023-12-15
 |  |  | Broušení | 0.50 | 2023-12-16
 |  |  | Svařování | 0.25 | 2023-12-20
 |  |  | Svařování | 2.50 | 2023-12-21
 |  |  | Svařování a broušení | 0.25 | 2023-12-22
 |  |  | Tisk | 1.00 | 2023-12-22
 |  |  | Svařování | 1.75 | 2023-12-23
 |  |  | Broušení | 1.50 | 2023-12-24
 |  |  | Broušení | 1.00 | 2023-12-25
 |  |  | Svařování a broušení | 2.50 | 2023-12-27
 |  |  | Vrtání a tvorba závitů | 1.00 | 2023-12-28
 |  |  | Svařování a broušení | 2.25 | 2023-12-30
 |  |  | Vrtání a tvorba závitů | 1.25 | 2023-12-31
 |  |  | Natáčení | 0.25 | 2023-12-31
 |  |  | Svařování | 0.50 | 2024-01-05
 |  |  | Svařování | 3.25 | 2023-01-06
 |  |  | Skládání konstrukce | 1.00 | 2024-01-06
 |  |  | Svařování a broušení | 1.25 | 2024-01-07
 |  |  | Vrtání | 0.75 | 2024-01-07
 |  |  | Skládání konstrukce | 1.75 | 2024-01-07
 |  |  | Nastavování servomotorů | 1.50 | 2024-02-21
 |  |  | Hledání chyb v konstrukci | 3.00 | 2024-02-22
 |  |  | Skládání konstrukce | 2.00 | 2024-02-23
 |  |  | Skládání konstrukce | 0.45 | 2024-02-24
Tvorba schéma | 2.00 | 2024-04-06 | Tvorba PCB | 4.00 | 2024-05-29
Tvorba schéma | 3.00 | 2024-04-18 | Tvorba PCB | 1.50 | 2024-05-30
Tvorba schéma | 1.50 | 2024-04-24 | Test a programování | 0.75 | 2024-05-30
Tvorba schéma | 5.00 | 2024-04-28 | Test a programování | 3.00 | 2024-06-06
Tvorba schéma | 1.00 | 2024-04-30 | Finální test rapoukTestBoardv0 | 2.50 | 2024-06-09
Tvorba schéma | 2.00 | 2024-05-06 | Měření | 1.00 | 2024-06-12
Tvorba schéma | 1.00 | 2024-05-13 | Úprava a příprava PCB | 1.50 | 2024-07-31
Tvorba schéma | 1.00 | 2024-05-14 | Tvorba PCB | 1.50 | 2024-08-13
Tvorba schéma | 2.50 | 2024-05-15 | Tvorba PCB | 2.50 | 2024-08-14
Tvorba schéma | 1.75 | 2024-05-16 | Tvorba PCB | 3.50 | 2024-08-18
Tvorba schéma | 2.00 | 2024-05-19 | Tvorba PCB | 2.00 | 2024-08-20
Tvorba schéma | 1.50 | 2024-06-10 | Tvorba PCB | 1.00 | 2024-08-21
Tvorba schéma | 1.00 | 2024-06-12 | Testování PCB | 2.00 | 2024-08-21
Tvorba schéma | 3.50 | 2024-06-14 | Oprava PCB | 1.00 | 2024-08-22
Tvorba schéma | 2.50 | 2024-06-16 | Testování nabíjení | 2.00 | 2024-08-27
Tvorba schéma | 2.00 | 2024-06-17 | Dorozumívání se s čínským datasheetem | 1.50 | 2024-08-28
Tvorba schéma | 1.00 | 2024-06-18 | Rychlonabíjení | 3.00 | 2024-08-30
Tvorba schéma | 2.00 | 2024-06-19 | Rychlonabíjení | 1.75 | 2024-09-01
Tvorba schéma | 0.50 | 2024-06-20 | Bezdrátové nabíjení | 1.50 | 2024-09-13
VSCode | 1.50 | 2024-06-26 | Bezdrátové nabíjení | 4.00 | 2024-09-22
Web | 1.00 | 2024-06-28 | Bezdrátové nabíjení | 1.50 | 2024-09-25
AI | 1.00 | 2024-07-16 | Bezdrátové nabíjení | 0.50 | 2024-10-09
Webová stránka | 3.00 | 2024-07-17 | Obrábění formy | 3.50 | 2024-11-08
Webová stránka | 1.50 | 2024-07-20 | Výroba PCB žehličky | 4.00 | 2024-11-11
Webová stránka | 5.50 | 2024-07-21 | Tranzistorový spínač | 0.75 | 2024-11-15
Testování SW | 2.50 | 2024-07-22 | Výroba PCB žehličky | 2.50 | 2024-11-17
Webová stránka | 2.50 | 2024-07-23 | Výroba PCB žehličky | 1.25 | 2024-11-18
SW | 2.00 | 2024-07-24 | Obrábění formy | 1.50 | 2024-11-21
Webová stránka | 1.00 | 2024-07-24 | Tisk formy | 1.00 | 2024-11-26
SW | 3.00 | 2024-07-26 | Výroba PCB žehličky | 1.00 | 2024-11-26
SW | 1.50 | 2024-07-27 | Příprava na výrobu PCB | 1.00 | 2024-11-26
SW | 1.50 | 2024-07-28 | Tvorba PCB | 5.50 | 2024-11-27
SW | 1.75 | 2024-07-29 | 3D tisk | 1.50 | 2024-11-28
Modelování a PCB | 1.50 | 2024-08-15 | Tvorba PCB | 3.50 | 2024-11-29
Modelování formy | 1.50 | 2024-08-16 | Tvorba PCB | 4.25 | 2024-12-01
Tvorba schéma | 3.00 | 2024-09-02 | Tvorba PCB | 4.00 | 2024-12-02
Tvorba schéma | 2.00 | 2024-09-03 | Tvorba PCB | 2.50 | 2024-12-03
Tvorba schéma | 1.75 | 2024-09-04 | Tesotvání PCB | 2.50 | 2024-12-07
Tvorba schéma | 1.00 | 2024-09-07 | Tesotvání PCB | 1.00 | 2024-12-08
Měření LED | 0.50 | 2024-09-08 | Úprava a příprava PCB | 2.25 | 2024-12-21
Tvorba schéma | 0.50 | 2024-09-08 | Programování a algoritmizace | 4.25 | 2024-12-22
Tvorba schéma | 4.50 | 2024-09-09 | Programování a algoritmizace | 1.50 | 2024-12-23
Tvorba schéma | 2.75 | 2024-09-10 | Programování a algoritmizace | 1.50 | 2024-12-24
Tvorba schéma | 4.00 | 2024-09-17 | Obrábění | 4.50 | 2024-12-25
Tvorba schéma | 3.25 | 2024-09-19 | Příprava na eloxování | 1.00 | 2025-01-03
Tvorba schéma | 2.00 | 2024-09-27 | Příprava na eloxování | 3.00 | 2025-01-04
CAM | 2.00 | 2024-10-04 | Příprava na eloxování | 1.25 | 2025-01-12
Tvorba schéma | 1.00 | 2024-10-08 | Tisk a úprava modelu | 2.00 | 2025-01-14
Tvorba schéma | 1.00 | 2024-10-10 | Příprava na eloxování | 2.50 | 2025-01-19
Tvorba schéma | 1.50 | 2024-10-12 | KOM | 1.00 | 2025-01-21
Tvorba schéma | 1.00 | 2024-10-13 | Eloxování | 10.00 | 2025-01-21
Tvorba schéma | 1.50 | 2024-10-19 | Eloxování | 8.00 | 2025-01-22
Tvorba schéma | 4.50 | 2024-10-20 | Konzervace | 0.75 | 2025-01-28
Tvorba schéma | 1.00 | 2024-10-21 | Příprava na pogumování | 1.50 | 2025-01-31
Tvorba schéma | 1.50 | 2024-10-25 | Pogumování | 3.00 | 2025-02-01
Tvorba schéma | 2.25 | 2025-01-09 | Skládání | 2.25 | 2025-02-04
Tvorba schéma | 2.00 | 2025-01-10 | Vakuové tvarování | 1.50 | 2025-02-06
Tvorba schéma | 2.50 | 2025-01-11 | Skládání | 1.00 | 2025-02-08
Tvorba schéma | 0.30 | 2025-01-12 | Skládání | 3.00 | 2025-02-10
Modelování | 1.50 | 2025-01-13 | Servomotory | 2.00 | 2025-02-12
Protokol | 1.50 | 2025-01-24 | Debugování | 4.00 | 2025-02-13
Protokol | 2.50 | 2025-01-25 | Debugování | 2.00 | 2025-02-14
Protokol | 0.75 | 2025-01-26 | Debugování | 6.00 | 2025-02-15
Modelování | 2.25 | 2025-02-05 | Debugování | 1.50 | 2025-02-16
Programování | 0.75 | 2025-02-19 | Debugování | 3.50 | 2025-02-17
Programování | 3.00 | 2025-02-20 | Debugování | 1.50 | 2025-02-18
Programování | 4.00 | 2025-02-21 | Tvorba PCB | 3.00 | 2025-03-19
Programování | 2.00 | 2025-02-22 | Tvorba PCB | 2.50 | 2025-03-21
Programování | 3.00 | 2025-02-23 | Tvorba PCB | 5.00 | 2025-03-22
Programování | 3.00 | 2025-02-24 | Tvorba PCB | 2.00 | 2025-03-25
Programování | 2.00 | 2025-03-02 | Testování PCB | 1.00 | 2025-03-26
Programování | 5.00 | 2025-03-03 | Testování PCB | 1.00 | 2025-03-27
Programování | 3.00 | 2025-03-06 | Přidávání chladičů | 1.00 | 2025-03-31
Aktualizace firmware | 2.00 | 2025-03-30 | Skládání | 1.50 | 2025-04-01
Programování | 1.00 | 2025-04-10 | Testování | 2.00 | 2025-04-03
 |  |  | Přiřazování pohybů | 1.00 | 2025-04-04
 |  |  | Nevím, všechno už | 2.50 | 2025-04-06
 |  |  | Focení | 1.00 | 2025-04-11
 |  |  | Focení | 0.50 | 2025-04-18
Součet hodin | 252.75 |  | Součet hodin | 378.45
Celkově | 631.20 |  | Počet hodin ročníkové práce | 292.65
Počet dní | 796.00 |  | Počet hodin dlouhodobé práce | 338.55
Průměrný počet hodin denně | 0.793 |  | Den ukončení práce | 2025-05-28
Pr. počet hodin v prac. dnu | 2.083

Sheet: Součástky
ID | Name | Designator | Footprint | Q | Price | Pins
1 | T-DEAN | BT1 | T_DEAN | 1 |  | 2
2 | 470nF | C1 | C1206 | 1 | $0.02 | 2
3 | 10uF | C2,C3,C4,C5,C6,C7,C12,C13,C16,C18,C22,C25 | C1206 | 12 | $0.20 | 2
4 | 3.3nF | C8 | C1206 | 1 | $0.02 | 2
5 | 100nF | C9,C11,C17,C19,C23,C24 | C1206 | 6 | $0.10 | 2
6 | 10uF | C10 | CAP-SMD_BD4.0-L4.3-W4.3-FD | 1 | $0.02 | 2
7 | 33nF | C14 | C1206 | 1 | $0.02 | 2
8 | 10nF | C15 | C1206 | 1 | $0.02 | 2
9 | 22uF | C20,C21 | C1206 | 2 | $0.03 | 2
10 | PH-6P立贴 | CN1 | CONN-SMD_6P-P2.0-L14.0-W5.4 | 1 | $0.02 | 8
11 | XH2.54-2AB | CN2 | CONN-SMD_2P-P2.54_XH2.54-2AB | 1 | $0.02 | 4
12 | XH2.54-3AB | CN3 | CONN-SMD_3P-P2.54_XH2.54-3AB | 1 | $0.02 | 5
13 | PH2.0-2P | CN4 | CONN-SMD_PH2.0-1X2PW | 1 | $0.02 | 4
14 | PH-4P立贴 | CN5 | CONN-SMD_PH2.0-4P | 1 | $0.02 | 6
15 | 2.0-3P | CN6 | CONN-SMD_3P-LT | 1 | $0.02 | 5
16 | SS54C | D1,D5 | SMC_L7.5-W5.8-LS8.3-RD | 2 | $0.03 | 2
17 | SS34-A | D2,D3,D4 | SMA_L4.3-W2.6-LS5.2-RD | 3 | $0.05 | 2
18 | 10uH | L1 | IND-SMD_L7.3-W7.3 | 1 | $0.02 | 2
19 | SINC1313-470M L470 SMD | L2 | SINC1313 | 1 |  | 2
20 | 15uH | L3 | IND-SMD_L10.2-W10.0 | 1 | $0.48 | 2
21 | 2.2uH | L4 | IND-SMD_L10.5-W10.5 | 1 | $0.55 | 2
22 | ŽLUTÁ | LED1 | LED1206-R-RD_RED | 1 | $0.55 | 2
23 | ZELENÁ | LED2 | LED1206-R-RD_RED | 1 | $0.55 | 2
24 | ČERVENÁ | LED3 | LED1206-R-RD_RED | 1 | $0.55 | 2
25 | MODRÁ | LED4 | LED1206-R-RD_RED | 1 | $0.55 | 2
26 | 1.2MΩ | R1 | R0603 | 1 | $0.55 | 2
27 | 3kΩ | R2 | R1206 | 1 | $0.55 | 2
28 | 15kΩ | R3 | R1206 | 1 | $0.55 | 2
29 | 510Ω | R4,R21 | R1206 | 2 | $1.10 | 2
30 | 100Ω | R5,R20 | R1206 | 2 | $1.10 | 2
31 | 10kΩ | R6,R15,R16,R17,R29,R31 | R1206 | 6 | $3.30 | 2
32 | 20kΩ | R7 | R1206 | 1 | $0.55 | 2
33 | 4.7kΩ | R8 | R1206 | 1 | $0.55 | 2
34 | 6.34kΩ | R9 | R1206 | 1 | $0.55 | 2
35 | 2kΩ | R10 | R1206 | 1 | $0.55 | 2
36 | 5.1kΩ | R11,R12,R30 | R0603 | 3 | $1.65 | 2
37 | 100kΩ | R13,R19 | R1206 | 2 | $1.10 | 2
38 | 6.8kΩ | R14 | R1206 | 1 | $0.55 | 2
39 | 47kΩ | R18 | R1206 | 1 |  | 2
40 | 470Ω | R22,R32 | R1206 | 2 | $0.03 | 2
41 | 82kΩ | R23 | R1206 | 1 | $0.02 | 2
42 | 1kΩ | R24,R25,R26 | R1206 | 3 | $0.05 | 2
43 | 60kΩ | R27 | R1206 | 1 | $0.02 | 2
44 | 0,5Ω | R28 | R1206 | 1 | $0.02 | 2
45 | TL3330AF130QG | SW1 | SW-SMD_E-SWITCH_TL3330 | 1 | $0.02 | 4
46 | ME3116 | U1 | SOT-23-6_L2.9-W1.6-P0.95-LS2.8-BL | 1 | $0.02 | 6
47 | XL4015E1 | U2 | TO-263-5_L10.2-W8.9-P1.70-TL | 1 | $0.02 | 6
48 | 220uF | U3,U4 | CAP-SMD_BD6.3-L6.6-W6.6-FD | 2 | $0.03 | 2
49 | S8050W | U5,U8 | SOT-323-3_L2.1-W1.3-P1.30-LS2.3-BR | 2 | $0.03 | 3
50 | XKT-3169 | U6 | SOIC-8_L4.9-W3.9-P1.27-LS6.0-BL | 1 | $0.02 | 9
51 | CH340C | U7 | SOP-16_L10.0-W3.9-P1.27-LS6.0-BL | 1 | $0.02 | 16
52 | 2.4GHz | U9 | WIRELM-SMD_ESP32-S | 1 | $0.02 | 39
53 | IP2326 | U10 | VQFN-24_L4.0-W4.0-P0.50-BL-EP2.5 | 1 | $0.02 | 25
54 | FSUSB42MUX | U11 | MSOP-10_L3.0-W3.0-P0.50-LS5.0-BL | 1 | $0.02 | 10
55 | AOD423 | U12 | TO-252-2_L6.6-W6.1-P4.60-LS10.0-BR-CW | 1 | $0.02 | 3
56 | Header-Male-2.54-3x8 | J1 | HDR-TH-3X8P-P2.54-V | 1 |  | 24
57 | Chladič na XL4015E1 |  |  | 1
 |  |  |  | 92 | $16.85
 |  |  |  |  | 405.92 Kč

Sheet: Finance
Koupené | Cena bez DPH | Ze skladu | Cena bez DPH
Šrouby | 90.00 Kč | Elektronika | 3000.00 Kč
Matice | 120.00 Kč | Krok. motory | 1600.00 Kč
5× Fréza | 300.00 Kč | Materiál
Technický líh | 360.00 Kč | Materiál na spojky | 250.00 Kč
Elektronika rapouk | 324.00 Kč | Vřeteno | 3000.00 Kč
Měniče | 50.00 Kč | Arduino a shield | 500.00 Kč
2× Závitník M2×0,4 | 274.00 Kč | 3D tisk | 50.00 Kč
Vratidlo | 93.00 Kč | Zdroje k CNC | 1000.00 Kč
řezací olej Al | 175.00 Kč | Kabeláž | 1500.00 Kč
Battery pack a nabíječka | 250.00 Kč
Doplnění argonu | 1250.00 Kč
Hliníkový přídavný materiál | 600.00 Kč
Prototyp PCB | 50.00 Kč
Nové servomotory | 1051.50 Kč
Celkem | 4987.50 Kč | Celkem | 10900.00 Kč

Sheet: Materiály
 | ABS (3D tisk) | Ocel | Nerezová ocel | Hliník | Titanzinek
Obrobitelnost | Jednoduchá | Jednoduchá | Jednoduchá | Složitá | Jednoduchá | https://www.kondor.cz/plech-cerny-5mm-1x2m/d-78427/
Dostupnost | Ano | Ano | Ne | Ano | Ne | https://www.ehlinik.cz/plech-hladky-50x1000x2000270kg/pro-SHV0000101.html?_gl=1*n8qk6k*_up*MQ..
Koroze | Ne | Ano | Ne | Ne | Ne | https://e-shop.magsy.cz/nerezove-plechy/
Cena s DPH (Kč) | 550 | 3641 | 5802 | 3748 | 107962 | https://www.alza.cz/gearlab-abs-3d-filament-2-85mm-d6697702.htm
 |  |  |  |  |  | https://evek.vip/titan/2105-176760-titanov--plech-t-dy-5-5-mm-titanov--plech-37165-titanov--plech--ezan--100-mm-a--2000-mm.html

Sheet: Ohyb
Zadání | Značky (jednotky) | Hodnota | Legenda
Délka servomotru | Ld (mm) | 40 | Zadání
Průměr | d (mm) | 4.6 | Výpočet
Gravitační zrychlení | G (m/s2) | 9.81
Maximální napětí v ohybu | σdo (MPa) | 60
Procento napětí |  | 10%
Počet noh |  | 4
OHYB
Napětí v ohybu | σo (MPa) | 6.000
Síla na jedné noze | F1 (N) | 5.734
Maximální zatížení na jedné noze | m1(kg) | 0.584
Síla celkem | F (N) | 22.934
Maximální zatížení | m (kg) | 2.338

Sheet: Step per
Úhel kroku | 1.8 | °
Stoupání závitové tyče | 5 | mm
Počet mezikroků | 8
Step per | 320

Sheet: Řezné podmínky
Zadání | Značka (jednotky) | Hodnota | Legenda
Otáčky | n (min-1) | 4260 | Zadání
Průměr nástroje | D (mm) | 3.125 | Výpočet
Počet zubů | z | 1
Posuv na zub | fz (mm) | 0.02
Řezná rychlost | Vc (m*min-1) | 41.8224522
Rychlost posuvu | Vf (mm*min-1) | 85.2
Posuv na otáčku | Fot (mm) | 0.02

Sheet: Odpor
Zadání | Značky (jednotky) | Hodnota | Legenda
Napětí obvodu | U0 (V) | 12 | Zadání
Provozní napětí diody | ULED (V) | 3.2 | Výpočet
Provozní proud | ILED (A) | 0.02
Odpor diody | RLED (Ω) | 160
Proud obvodu | I0 (A) | 0.02
Napětí na odporu | UR (V) | 8.8
Odpor rezistoru | R (Ω) | 440
Výkon rezistoru | P (W) | 0.176

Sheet: Výdrž baterie
Zadání | Značky (jednotky) | Hodnota | Legenda
Napětí | U (V) | 8.4 | Zadání
Proud | I (A) | 2.3 | Výpočet
Kapacita baterie | Ib (Ah) | 3.4
Výkon baterie | Pb (Wh) | 28.56
Výdrž baterie | t (h) | 1.47826087

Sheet: Voltmetr
Maximální napětí baterie | Vbat (V) | 36.3
Maximální napětí ovl. Desky | Vin (V) | 3.3
Odpor | R1 (kΩ) | 10
Odpor | R2 (kΩ) | 100
https://www.youtube.com/watch?v=gw72g4WBz-U

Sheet: Křivky
 |  | Procento
1 | 8.4 | 328.6555648
2 | 8.2 | 298.1768864
3 | 7.6 | 186.7492352
4 | 7.5 | 167.3828125
5 | 7.4 | 150.2518048
6 | 7.2 | 125.2363264
7 | 7 | 111.59
8 | 6.8 | 97.1201536

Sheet: List1
8.4 | 8.2 | 7.6 | 7.5 | 7.4 | 7.2 | 7.0 | 6.8
5040 | 4540 | 1740 | 990 | 640 | 140 | 65 | 0
100 | 90.1 | 34.5 | 19.6 | 12.7 | 2.8 | 1.3 | 0

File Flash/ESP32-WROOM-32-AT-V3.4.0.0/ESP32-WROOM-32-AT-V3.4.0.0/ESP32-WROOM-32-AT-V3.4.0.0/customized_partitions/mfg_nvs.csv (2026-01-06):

key | type | encoding | value
server_cert | namespace
server_cert | file | binary | /builds/application/esp-at/components/customized_partitions/raw_data/server_cert/server_cert.crt
server_key | namespace
server_key | file | binary | /builds/application/esp-at/components/customized_partitions/raw_data/server_key/server.key
server_ca | namespace
server_ca | file | binary | /builds/application/esp-at/components/customized_partitions/raw_data/server_ca/server_ca.crt
client_cert | namespace
client_cert.0 | file | binary | /builds/application/esp-at/components/customized_partitions/raw_data/client_cert/client_cert_00.crt
client_cert.1 | file | binary | /builds/application/esp-at/components/customized_partitions/raw_data/client_cert/client_cert_01.crt
client_key | namespace
client_key.0 | file | binary | /builds/application/esp-at/components/customized_partitions/raw_data/client_key/client_key_00.key
client_key.1 | file | binary | /builds/application/esp-at/components/customized_partitions/raw_data/client_key/client_key_01.key
client_ca | namespace
client_ca.0 | file | binary | /builds/application/esp-at/components/customized_partitions/raw_data/client_ca/client_ca_00.crt
client_ca.1 | file | binary | /builds/application/esp-at/components/customized_partitions/raw_data/client_ca/client_ca_01.crt
mqtt_cert | namespace
mqtt_cert | file | binary | /builds/application/esp-at/components/customized_partitions/raw_data/mqtt_cert/mqtt_client.crt
mqtt_key | namespace
mqtt_key | file | binary | /builds/application/esp-at/components/customized_partitions/raw_data/mqtt_key/mqtt_client.key
mqtt_ca | namespace
mqtt_ca | file | binary | /builds/application/esp-at/components/customized_partitions/raw_data/mqtt_ca/mqtt_ca.crt
factory_param | namespace
version | data | i8 | 4
module_name | data | string | WROOM-32
max_tx_power | data | i8 | 78
country_code | data | string | CN
start_channel | data | u8 | 1
channel_num | data | u8 | 13
uart_port | data | i8 | 1
uart_baudrate | data | i32 | 115200
uart_tx_pin | data | i32 | 17
uart_rx_pin | data | i32 | 16
uart_cts_pin | data | i32 | 15
uart_rts_pin | data | i32 | 14
ble_data | namespace
cfg0 | data | string | 0,16,0x2800,0x01,2,2,A002
cfg1 | data | string | 1,16,0x2803,0x01,1,1,02
cfg2 | data | string | 2,16,0xC300,0x01,1,1,30
cfg3 | data | string | 3,16,0x2901,0x11,1,1,30
cfg4 | data | string | 4,16,0x2803,0x01,1,1,02
cfg5 | data | string | 5,16,0xC301,0x01,512,512,
cfg6 | data | string | 6,16,0x2901,0x11,512,512,
cfg7 | data | string | 7,16,0x2803,0x01,1,1,08
cfg8 | data | string | 8,16,0xC302,0x10,1,1,30
cfg9 | data | string | 9,16,0x2901,0x01,1,1,01
cfg10 | data | string | 10,16,0x2803,0x01,1,1,04
cfg11 | data | string | 11,16,0xC303,0x10,1,1,30
cfg12 | data | string | 12,16,0x2901,0x10,1,1,30
cfg13 | data | string | 13,16,0x2803,0x01,1,1,08
cfg14 | data | string | 14,16,0xC304,0x10,512,512,
cfg15 | data | string | 15,16,0x2803,0x01,1,1,10
cfg16 | data | string | 16,16,0xC305,0x01,1,1,00
cfg17 | data | string | 17,16,0x2902,0x11,2,2,0000
cfg18 | data | string | 18,16,0x2803,0x01,1,1,20
cfg19 | data | string | 19,16,0xC306,0x01,1,1,00
cfg20 | data | string | 20,16,0x2902,0x11,2,2,0000
cfg21 | data | string | 21,16,0x2803,0x01,1,1,02
cfg22 | data | string | 22,16,0xC307,0x01,1,1,30
cfg23 | data | string | 23,16,0x2901,0x11,256,1,30
cfg24 | data | string | 24,16,0x2800,0x01,2,2,A003
cfg25 | data | string | 25,16,0x2803,0x01,1,1,02
cfg26 | data | string | 26,16,0xC400,0x01,1,1,30
cfg27 | data | string | 27,16,0x2901,0x11,1,1,30
cfg28 | data | string | 28,16,0x2803,0x01,1,1,02
cfg29 | data | string | 29,16,0xC401,0x01,1,1,30
cfg30 | data | string | 30,16,0x2901,0x11,256,1,30

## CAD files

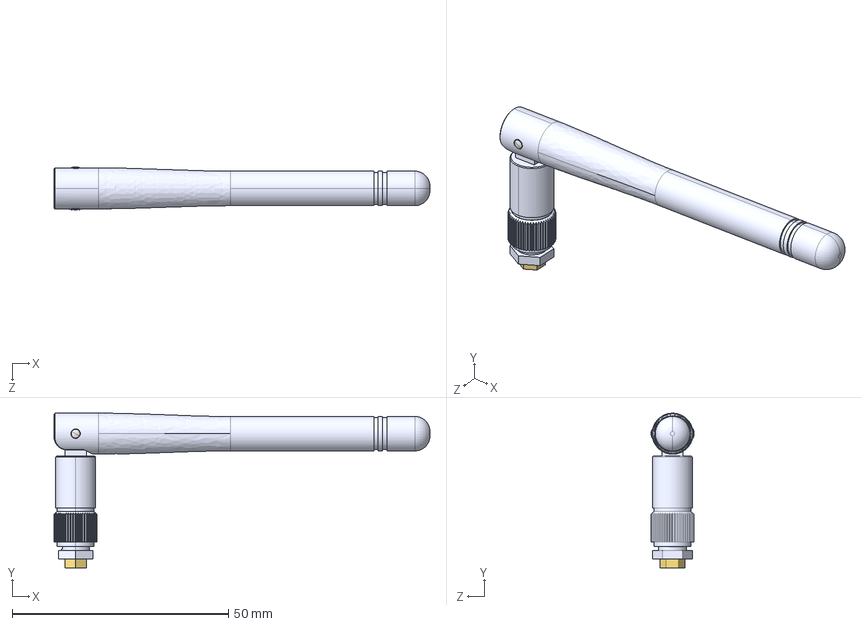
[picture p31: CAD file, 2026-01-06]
Technical documentation/Final/1assemble antenn.STEP
87.0 x 35.8 x 10.0 mm
antenn2
antenn1
taper pin unhardened_iso_ISO 2339 - A - 2 x 10 - St

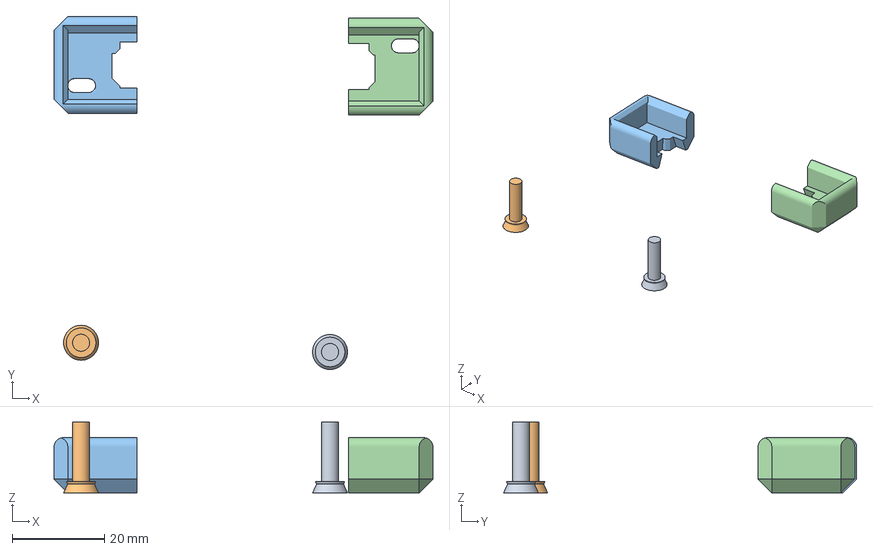
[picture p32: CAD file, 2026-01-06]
CAM/rapoukPrintFDMv0.3mf
82.2 x 76.6 x 15.4 mm
rapoukStickv0.stl x 2
rapoukCupLv0.stl
rapoukCupRv0.stl

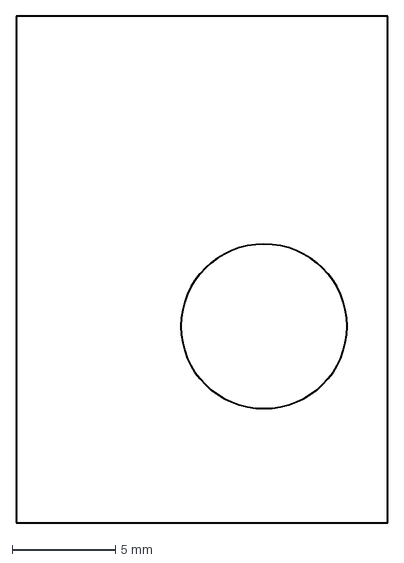
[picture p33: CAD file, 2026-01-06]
DXF/Final/rapoukLegBasev3.dxf
18.0 x 24.5 mm

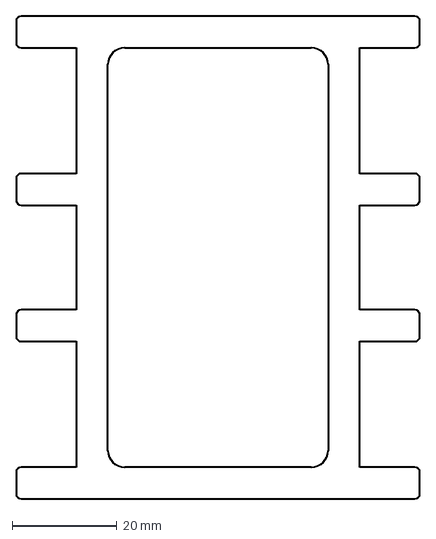
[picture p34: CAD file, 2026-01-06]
Gcode/SD/DXF/rapoukBasev4CNC.dxf
77.0 x 92.0 mm

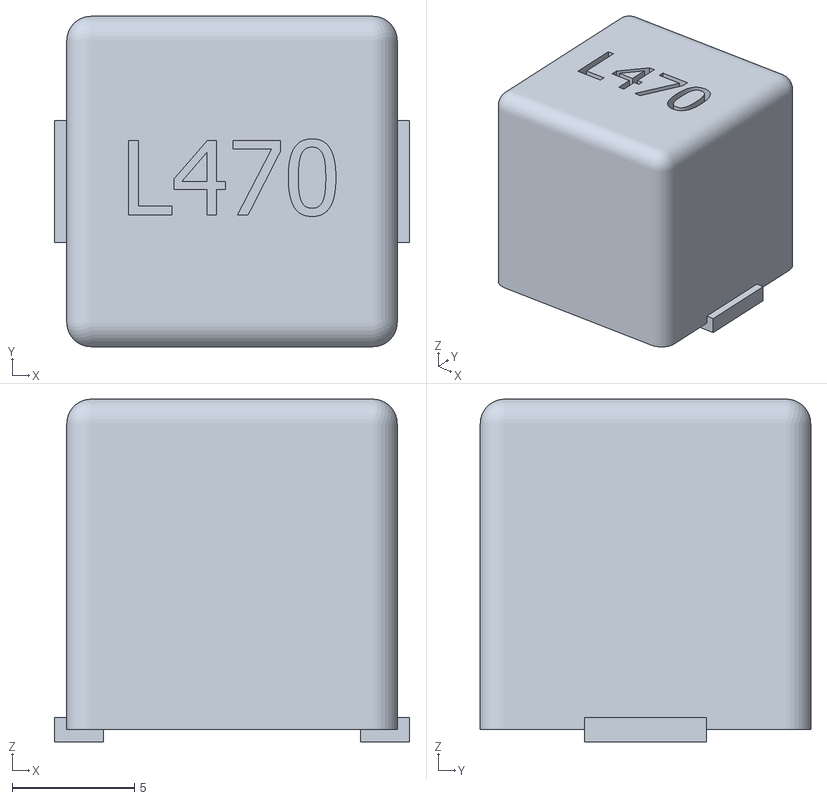
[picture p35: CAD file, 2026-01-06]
SINC/SINC1313-470_L470_SMD.stl
14.5 x 13.5 x 14.0

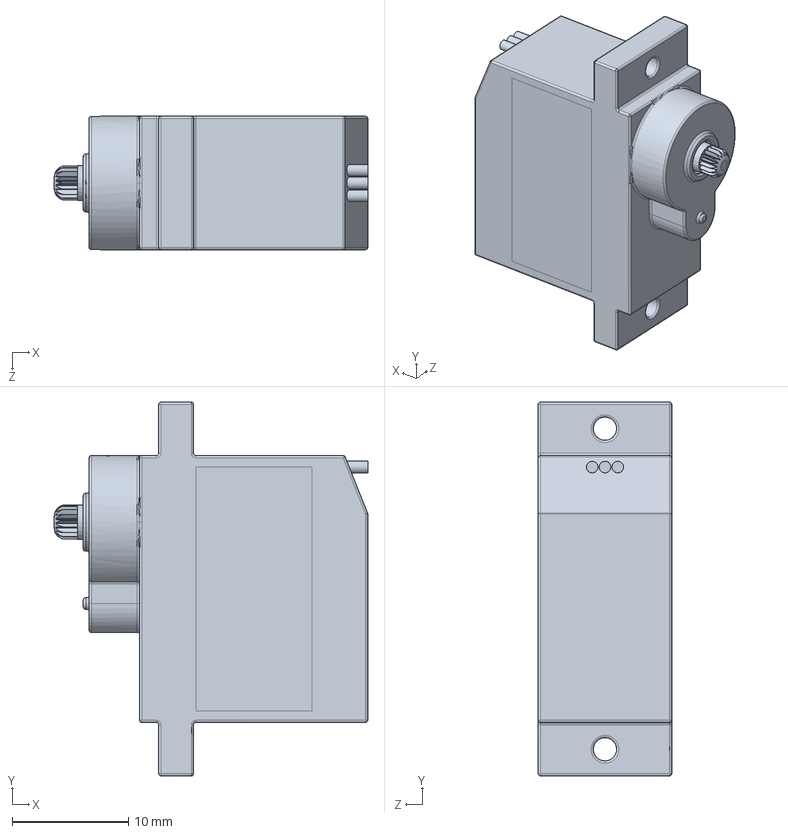
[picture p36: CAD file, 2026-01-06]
Technical documentation/anotherFinalIThinkxD/сервопривод EMAX ES08MA.SLDPRT
27.0 x 32.2 x 11.5 mm

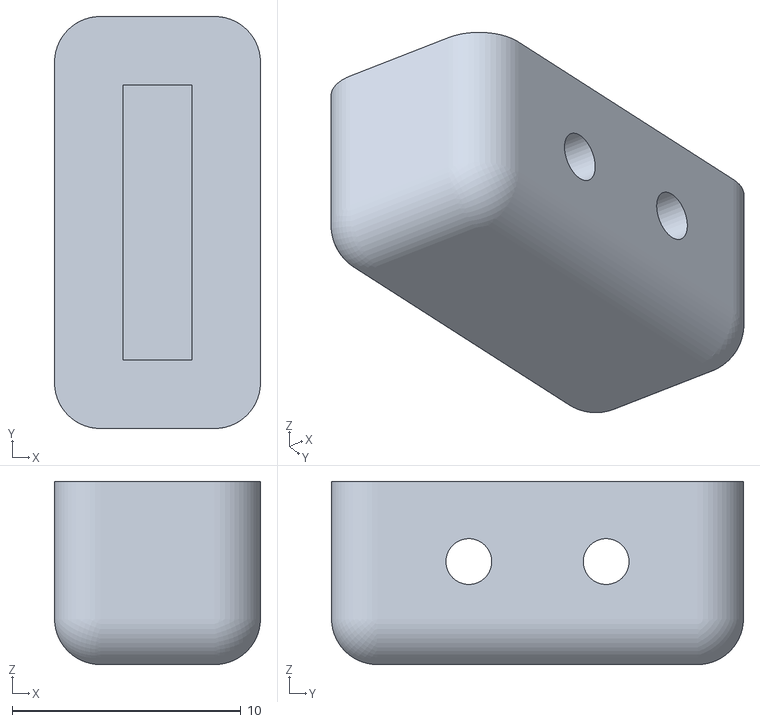
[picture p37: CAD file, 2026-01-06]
Technical documentation/drill/3mm.stl
9.00 x 18.0 x 8.00

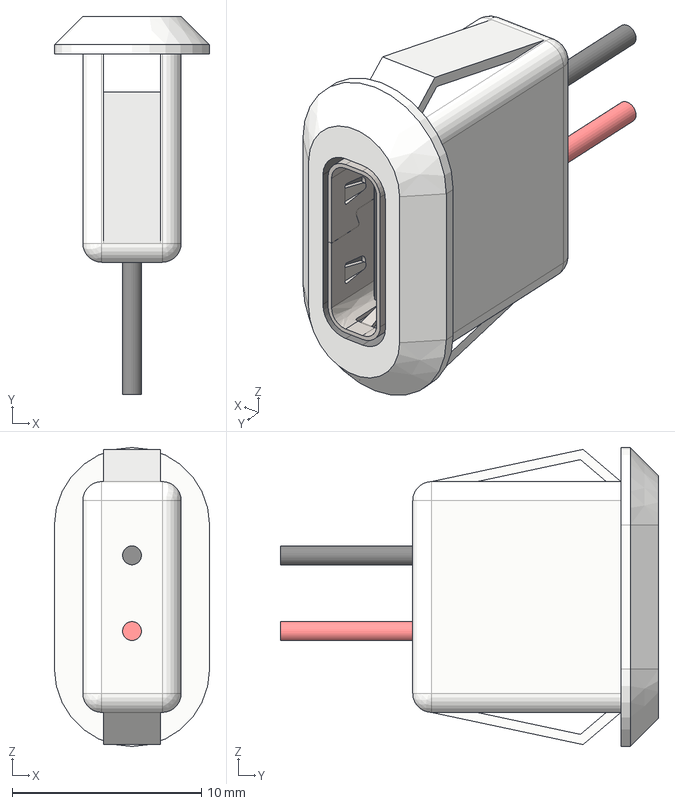
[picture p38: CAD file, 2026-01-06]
Technical documentation/Final/type c jack connector.step
8.20 x 20.0 x 15.8 mm
USB Connector Type C female

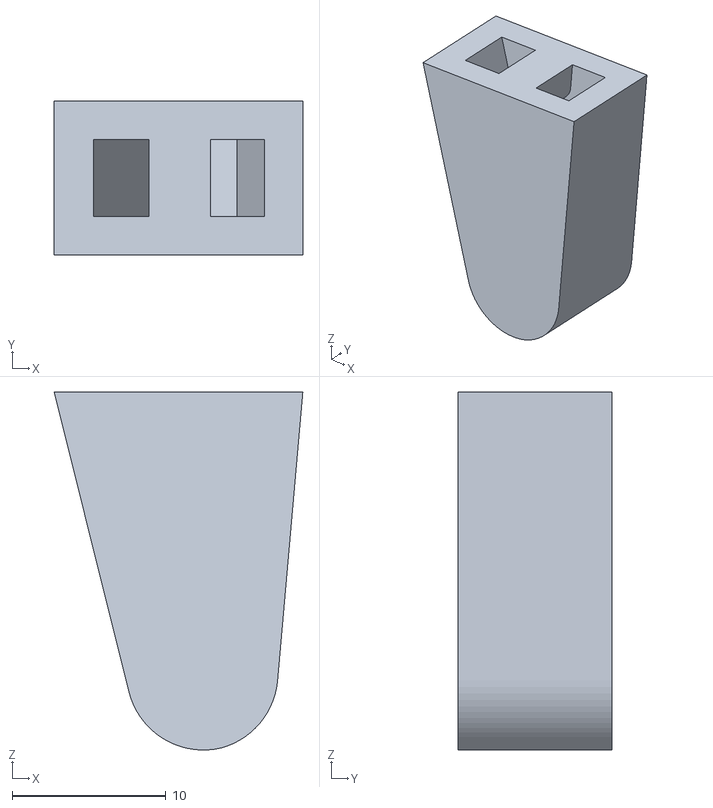
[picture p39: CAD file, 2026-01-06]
Technical documentation/mould/volume.stl
16.2 x 10.0 x 23.3

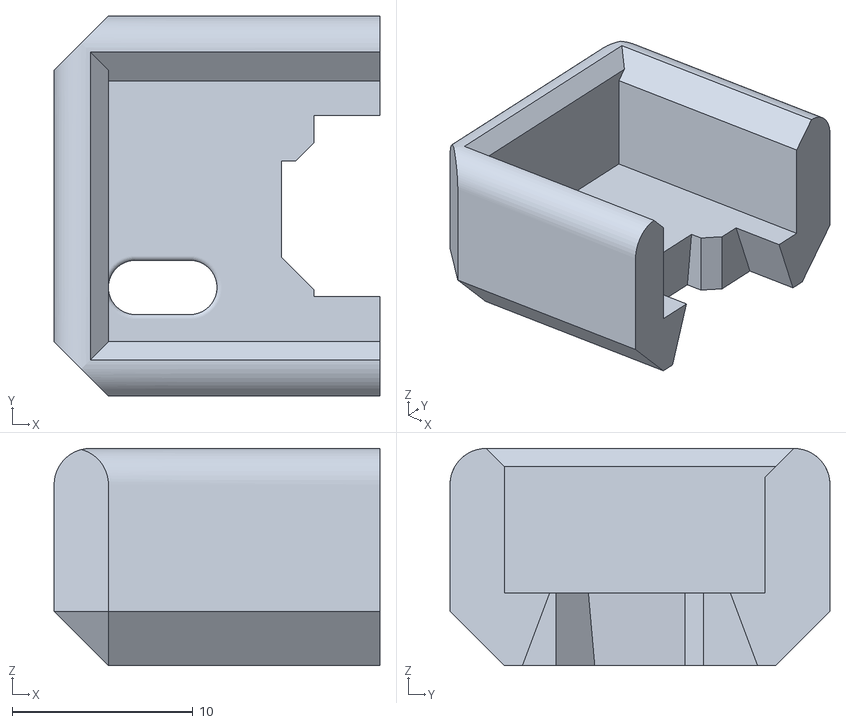
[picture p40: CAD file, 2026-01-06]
CAM/rapoukCupLv0.stl
18.0 x 21.0 x 12.0

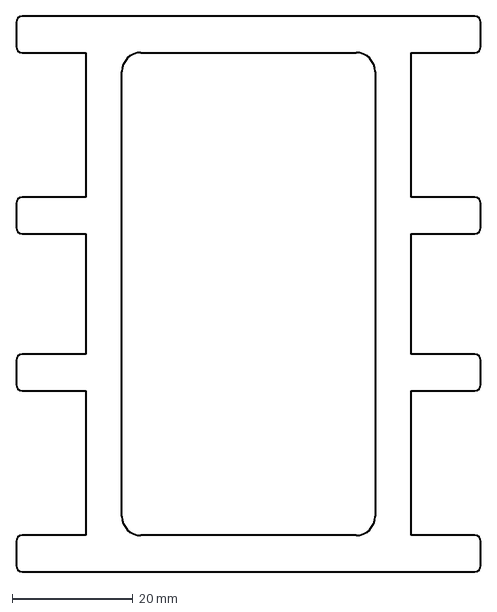
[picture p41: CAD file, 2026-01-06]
DXF/Final/rapoukBasev4CNC.dxf
77.0 x 92.0 mm

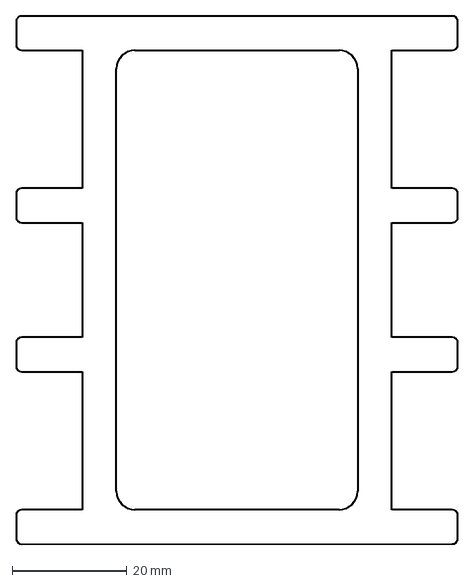
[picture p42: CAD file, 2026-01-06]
Gcode/SD/DXF/rapoukBasev4.dxf
77.0 x 92.0 mm

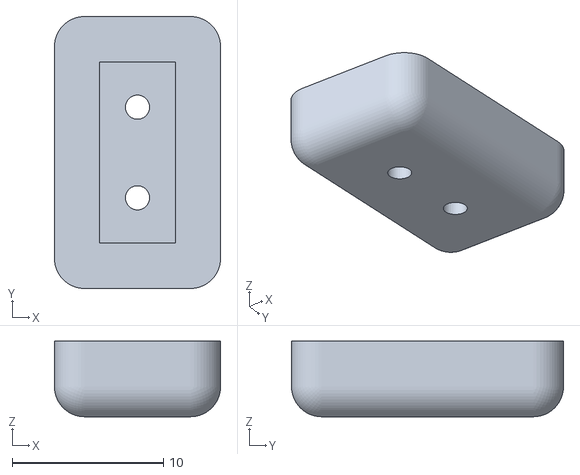
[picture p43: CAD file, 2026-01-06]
Technical documentation/drill/5mm.stl
11.0 x 18.0 x 5.00

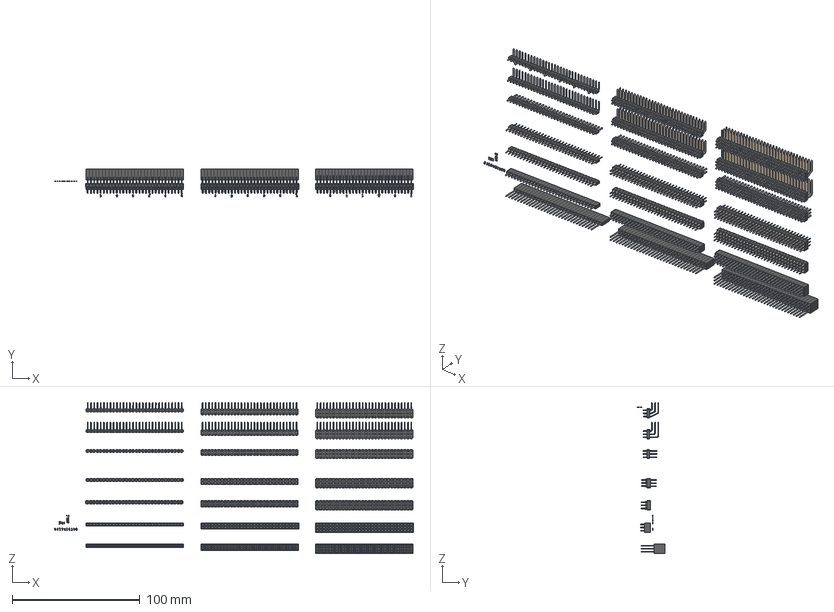
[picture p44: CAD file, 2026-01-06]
Technical documentation/Final/PINS-SET.stp
281.4 x 22.1 x 118.5 mm
Number
NOT
num Geometry x 3
F-1Row Geometry
pin x 30
pin-dn x 30
F-2Row Geometry
F-3Row Geometry

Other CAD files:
DXF/rapoukLegv9.dwg
DXF/rapoukMiddleLeg0v3.dwg
SINC/SINC1313-470_L470_SMD_G.obj
Technical documentation/mould/rapoukMouldBottomv0.stl
CAM/CAM.ipt
CAM/CAM3D.ipt
CAM/rapoukCupRv0.stl
CAM/rapoukPrintSLSv0.3mf
CAM/rapoukStickv0.stl
DXF/Final/rapoukLegPinv1.dxf
DXF/Final/rapoukLegSupportv1.dxf
DXF/Final/rapoukLegSupportv2.dxf
DXF/Final/rapoukLegv9.dxf
DXF/Final/rapoukMiddleLeg0v3.dxf
DXF/Final/rapoukMiddleLeg1v3.dxf
DXF/Final/rapoukMiddleLeg2v3.dxf
DXF/Final/rapoukMiddleLeg2v3Multi.dxf
DXF/Final/ring.dxf
DXF/Final/topLegBasev1.dxf
DXF/OldVersions/rapoukLegBasev3.0001.dwg
DXF/OldVersions/rapoukMiddleLeg0v3-1.0001.dwg
DXF/OldVersions/rapoukMiddleLeg0v3-1.0001_1.dwg
DXF/OldVersions/rapoukMiddleLeg0v3.0001.dwg
DXF/line.dwg
DXF/line.dxf
DXF/rapoukLegBasev3.dwg
DXF/rapoukLegBasev3.dxf
DXF/rapoukLegPinv1.dwg
DXF/rapoukLegSupportv1.dwg
DXF/rapoukMiddleLeg1v3.dwg
DXF/rapoukMiddleLeg2v3.dwg
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

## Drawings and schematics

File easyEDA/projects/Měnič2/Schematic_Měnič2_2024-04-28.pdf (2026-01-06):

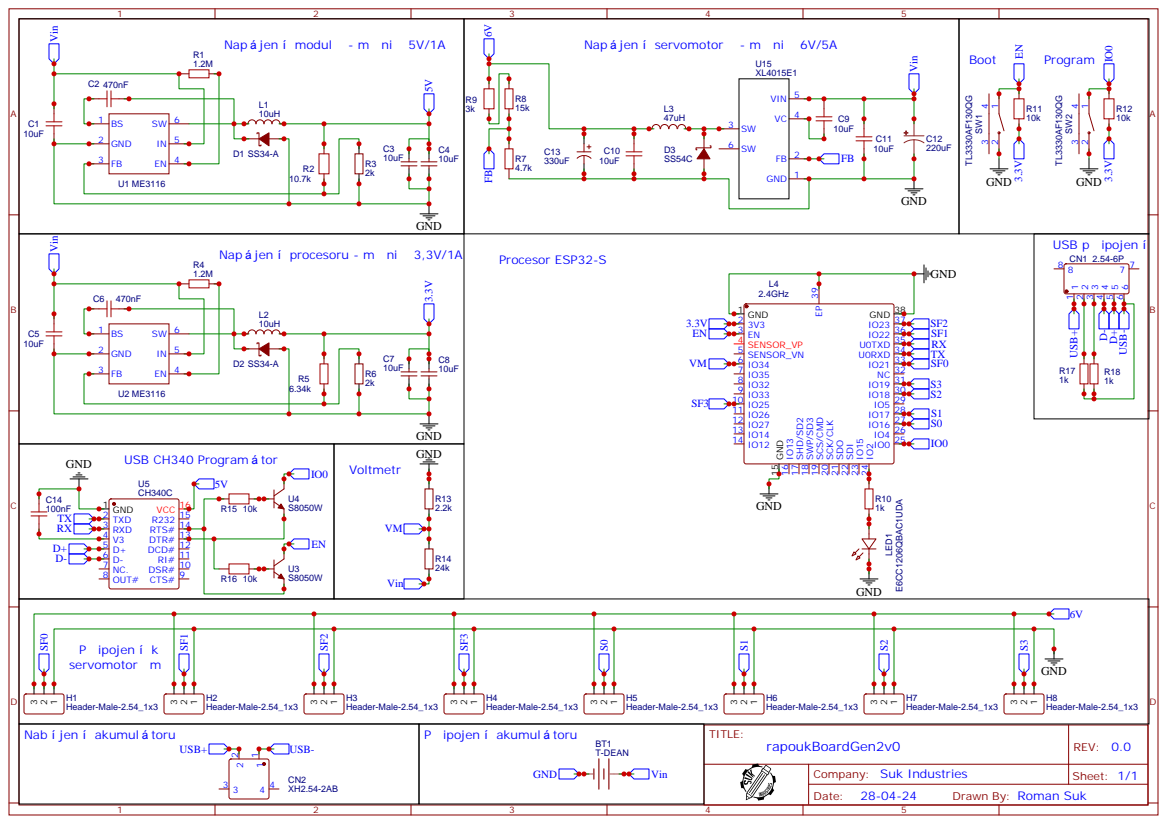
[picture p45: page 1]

Nap jen servomotor - m ni 6V/5A

DSR# 10 RI# 11 DCD# 12 DTR# 13 RTS# 14 R232 15 VCC 16

Drawn By: Roman Suk

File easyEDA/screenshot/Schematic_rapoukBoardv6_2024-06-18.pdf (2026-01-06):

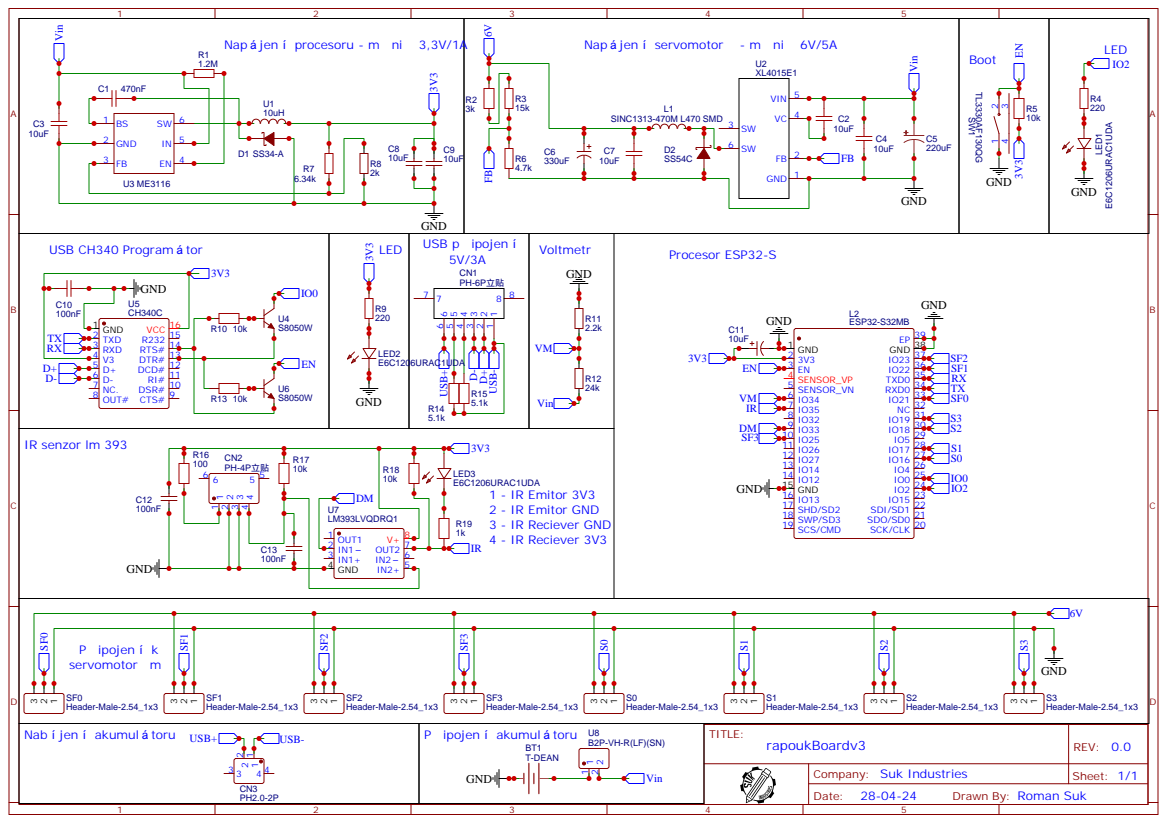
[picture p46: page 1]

Drawn By: Roman Suk

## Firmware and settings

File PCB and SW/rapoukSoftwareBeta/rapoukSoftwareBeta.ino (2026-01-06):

//Suk Industries Software Development
//Tato verze je verze z CD k DMP
//Jedná se o beta verzi základní funkce projektu Rapouk a proto všechny funkce nefungují správně
//Základní princtip DMP je funkční

#include <WiFi.h>
#include <AsyncTCP.h>
#include <ESPAsyncWebServer.h>
#include <ESP32Servo.h>
#include <Wire.h>
#include <Adafruit_VL6180X.h>

const char* ssid = "softAP-ESP32";
const char* password = "123456789";

Servo SF0, SF1, SF2, SF3, S0, S1, S2, S3;

#define LED 2
#define maxConnection 1
#define ADC 34
#define stopDelay 10

int lastStationCount=-1;
int defaultAngle=80;
int add=30;
int beginAngle0=0;
int beginAngle1=180-beginAngle0;
int stopAngle0=65;
int stopAngle1=180-stopAngle0;
int rightAngle0=120;
int rightAngle1=180-rightAngle0;

uint8_t setSpeed;
uint16_t highValue = 0;
uint16_t lowValue = 4095;
uint32_t sum = 0;
uint8_t percent = 0;
unsigned int i = -1;

bool tempomat;
bool setupCore;
bool moving;

String IP;

AsyncWebServer server(80);
Adafruit_VL6180X sensor = Adafruit_VL6180X();

unsigned long previousMillis = 0;

enum Animation {HOME, FORWARD, BACKWARD, TURNLEFT, TURNRIGHT, ROTATELEFT, ROTATERIGHT, HELLO, PUSHUP, WAVE, ANIMATION0, ANIMATION1, ANIMATION2, LIE, OFF};
Animation currentAnimation = LIE;
int lastAnimation;

const char html[] PROGMEM = R"rawliteral(
<!DOCTYPE html>
<html lang="cz">
<head>
    <meta charset="UTF-8">
    <title>Ovladání Rapouka</title>
    <style>
        body {
            display: flex;
            justify-content: center;
            align-items: center;
            height: 80vh;
            width: 95vw;
            background-color: #303134;
            font-family: 'Helvetica', 'Arial', sans-serif;
            -webkit-touch-callout: none;
            -webkit-user-select: none;
            -khtml-user-select: none;
            -moz-user-select: none;
            -ms-user-select: none;
            user-select: none;
            -webkit-tap-highlight-color: transparent;
            touch-action: none;
        }

        .container {
            display: flex;
            justify-content: space-between;
            width: 100%;
            padding: 0 20px;
        }

        .controller, .animations {
            display: grid;
            grid-gap: 10px;
            padding: 20px;
            background-color: #4c4c4c;
            border-radius: 10px;
            box-shadow: 0 0 10px #00000033;
        }

        .controller {
            grid-template-areas: 
                "rotateLeft moveForward rotateRight"
                "turnLeft home turnRight"
                ". moveBackward .";
            justify-items: center;
            align-items: center;
        }

        .animations {
            grid-template-areas: 
                "animationHello animationPushup animationWave"
                "animationCustom0 animationCustom1 animationCustom2";
            justify-items: center;
            align-items: center;
        }

        .settings {
            display: flex;
            flex-direction: column;
            align-items: center;
            justify-content: center;
            text-align: center;
            padding: 15px;
            background-color: #4c4c4c;
            border-radius: 10px;
            box-shadow: 0 0 10px #00000033;
        }

        .settings .setting-item {
            display: flex;
            align-items: center;
            justify-content: center;
            margin: 20px 0;
            font-size: x-large;
            accent-color: #af0808;
        }

        .settings .setting-item p {
            margin: 0;
            margin-right: 10px;
        }
        
        button {
            width: 100px;
            height: 100px;
            font-size: xx-large;
            cursor: pointer;
            border: none;
            border-radius: 10px;
            box-shadow: 0 2px 5px #00000033;
            transition: background-color 0.3s ease;
            color: white;
        }

        button:active {
            transform: scale(0.95);
        }

        .moveForward {grid-area: moveForward; background-color: #7C0A02;}
        .turnLeft {grid-area: turnLeft; background-color: #7C0A02;}
        .home {grid-area: home; background-color: #7C0A02;}
        .turnRight {grid-area: turnRight; background-color: #7C0A02;}
        .moveBackward {grid-area: moveBackward; background-color: #7C0A02;}

        .rotateLeft {grid-area: rotateLeft; background-color: #af0808;}
        .rotateRight {grid-area: rotateRight; background-color: #af0808;}

        .animationHello {background-color: #7C0A02; font-size: 275%;}
        .animationPushup {background-color: #7C0A02; font-size: 275%;}
        .animationWave {background-color: #7C0A02; font-size: 275%;}
        .animationCustom0 {background-color: #7C0A02; font-size: larger;}
        .animationCustom1 {background-color: #7C0A02; font-size: larger;}
        .animationCustom2 {background-color: #7C0A02; font-size: larger;}

        #content {
            display: none;
        }

        #warning {
            display: none;
            margin: 10%;
            text-align: center;
            font-size: 50px;
            color: #f70d1a;
        }

        @media (orientation: landscape) {
            #content {
                display: block;
            }

            #warning {
                display: none;
            }
        }

        @media (orientation: portrait) {
            #content {
                display: none;
            }

            #warning {
                display: block;
            }
        }

        .switch {
            position: relative;
            display: inline-block;
            width: 60px;
            height: 34px;
        }

        .switch input {
            opacity: 0;
            width: 0;
            height: 0;
        }

        .slider {
            position: absolute;
            cursor: pointer;
            top: 0;
            left: 0;
            right: 0;
            bottom: 0;
            background-color: #303134;
            -webkit-transition: .4s;
            transition: .4s;
        }

        .slider:before {
            position: absolute;
            content: "";
            height: 26px;
            width: 26px;
            left: 4px;
            bottom: 4px;
            background-color: #af0808;
            -webkit-transition: .4s;
            transition: .4s;
        }

        input:checked + .slider {
            background-color: #7C0A02;
        }

        input:focus + .slider {
            box-shadow: 0 0 3px #00000033;
        }

        input:checked + .slider:before {
            -webkit-transform: translateX(26px);
            -ms-transform: translateX(26px);
            transform: translateX(26px);
        }

        .slider.round {
            border-radius: 34px;
        }

        .slider.round:before {
            border-radius: 50%;
        }
    </style>
</head>
<body>
    <div id="content">
        <div class="container">
            <div class="controller">
                <button class="rotateLeft" data-command="rotateLeft">↺</button>
                <button class="moveForward" data-command="moveForward">↑</button>
                <button class="rotateRight" data-command="rotateRight">↻</button>
                <button class="turnLeft" data-command="turnLeft">←</button>
                <button class="home" data-command="home">■</button>
                <button class="turnRight" data-command="turnRight">→</button>
                <button class="moveBackward" data-command="moveBackward">↓</button>
            </div>
            <div class="settings">
                <div class="setting-item">
                    <p class="IP">IP adresa<br><span id="IPAdress">unknown</span></p>
                </div>
                <div class="setting-item">
                    <p>Aktuální % baterie<br><span id="batteryStatus">unknown</span></p>
                </div>
                <div class="setting-item">
                    <p>Tempomat</p>
                    <label class="switch">
                        <input type="checkbox" data-command="autopilot">
                        <span class="slider round"></span>
                    </label>
                </div>
                <div>
                    <p class="setting-item">Rychlost</p>
                    <input class="setting-item" style="width: 180px;" type="range" min="0" max="50" value="10" data-command="setSpeed">
                </div>
            </div>
            <div class="animations">
                <button class="animationHello" data-command="animationHello">👋</button>
                <button class="animationPushup" data-command="animationPushup">🖱️</button>
                <button class="animationWave" data-command="animationWave">🌊</button>
                <button class="animationCustom0" data-command="animationCustom0">Custom 0</button>
                <button class="animationCustom1" data-command="animationCustom1">Custom 1</button>
                <button class="animationCustom2" data-command="animationCustom2">Custom 2</button>
            </div>
        </div>
    </div>
    <div id="warning">
        <p>Otoč si zařízení na šířku!</p>
        <p>Tohle není Instagram 😆</p>
    </div>
    <script>
        let isBusy = false;
        let longPressTimer = null;
        let lastOffCommand = null;
        let autopilotEnabled = false;

        async function sendRequest(url) {
            try {
                const response = await fetch(url);
                if (!response.ok) throw new Error("Loading error: " + response.status);
                return await response.text();
            } catch (error) {}
        }

        async function toggleCheckbox(command, value) {
            if (isBusy && command !== "off") return;
            if (autopilotEnabled && !["batteryStatus", "autopilotOn", "setSpeed"].includes(command)) return;

            let url = `/${command}${value !== undefined ? `?value=${value}` : ""}`;

            if (command === "off" && lastOffCommand === url) return;
            lastOffCommand = command === "off" ? url : null;

            isBusy = true;
            await sendRequest(url);
            isBusy = false;
        }

        function handleLongPress(command, value) {
            longPressTimer = setInterval(() => {
                if (!isBusy) toggleCheckbox(command, value);
            }, 1000);
        }

        function cancelLongPress() {
            clearInterval(longPressTimer);
            longPressTimer = null;
        }

        function setupButtons() {
            document.querySelectorAll("[data-command]").forEach(button => {
                const command = button.getAttribute("data-command");
                const value = button.getAttribute("data-value");

                if (button.type === "range") {
                    button.addEventListener("input", () => toggleCheckbox(command, button.value));

                    if (command === "setSpeed") {
                        toggleCheckbox(command, button.value);
                    }

                } else {
                    const pressHandler = () => {
                        cancelLongPress();
                        toggleCheckbox(command, value);
                        handleLongPress(command, value);
                    };
                    const releaseHandler = () => {
                        cancelLongPress();
                        if (command !== "setSpeed") toggleCheckbox("off");
                    };

                    button.addEventListener("touchstart", pressHandler);
                    button.addEventListener("touchend", releaseHandler);
                    button.addEventListener("mousedown", pressHandler);
                    button.addEventListener("mouseup", releaseHandler);
                }
            });
        }

        async function updateElementContent(url, elementId, suffix = "") {
            const response = await sendRequest(url);
            if (response !== undefined) document.getElementById(elementId).innerText = response + suffix;
        }

        async function updateBatteryStatus() {
            const response = await sendRequest("/batteryStatus");
            if (response !== undefined) {
                const batteryStatus = parseInt(response);
                const batteryElement = document.getElementById("batteryStatus");
                batteryElement.innerText = batteryStatus + "%";
                batteryElement.style.color = batteryStatus <= 20 ? "red" : "black";
            }
        }

        function lockOrientation() {
            if (screen.orientation) {
                screen.orientation.lock("landscape").catch(() => {});
            }
        }

        function setupAutopilotSwitch() {
            const autopilotSwitch = document.querySelector("[data-command='autopilot']");
            if (autopilotSwitch) {
                autopilotSwitch.addEventListener("change", () => {
                    autopilotEnabled = autopilotSwitch.checked;
                    toggleCheckbox(autopilotEnabled ? "autopilotOn" : "autopilotOff");
                });
            }
        }

        window.addEventListener("load", () => {
            lockOrientation();
            updateElementContent("/IPAdress", "IPAdress");
            updateBatteryStatus();
            setInterval(updateBatteryStatus, 6000);
            setupAutopilotSwitch();
            setupButtons();
        });
    </script>
</body>
</html>
)rawliteral";
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
void loop() {
  if (WiFi.softAPgetStationNum()!=lastStationCount) {
    if (WiFi.softAPgetStationNum()==maxConnection) {
      Serial.println("Server full");
      //currentAnimation = HOME;
    } else {
      Serial.println("Server open");
      currentAnimation = LIE;
    }
    lastStationCount = WiFi.softAPgetStationNum();
  }
  if (tempomat) {
    unsigned long currentMillis = millis();
    if (currentMillis - previousMillis >= 100) {
      uint8_t range = sensor.readRange();
      uint8_t status = sensor.readRangeStatus();
      Serial.print("Tempomat - ");
      switch (status) {
        case VL6180X_ERROR_NONE:
          digitalWrite(LED, LOW);
          if (range <= 50) {
            currentAnimation = HOME;
            Serial.print("found an obstacle - ");
          } else {
            currentAnimation = FORWARD;
            Serial.print("measuring - ");
          }
          Serial.printf("Distance: %d mm\n", range);
          break;
        case VL6180X_ERROR_ECEFAIL:
          currentAnimation = HOME;
          digitalWrite(LED, HIGH);
          Serial.println("ECE failure");
          break;
        case VL6180X_ERROR_NOCONVERGE:
          currentAnimation = HOME;
          digitalWrite(LED, HIGH);
          Serial.println("no convergence");
          break;
        case VL6180X_ERROR_RANGEIGNORE:
          currentAnimation = HOME;
          digitalWrite(LED, HIGH);
          Serial.println("ignoring range");
          break;
        case VL6180X_ERROR_SNR:
          currentAnimation = HOME;
          digitalWrite(LED, HIGH);
          Serial.println("signal/noise error");
          break;
        case VL6180X_ERROR_RAWUFLOW:
          currentAnimation = HOME;
          digitalWrite(LED, HIGH);
          Serial.println("raw reading underflow");
          break;
        case VL6180X_ERROR_RAWOFLOW:
          currentAnimation = HOME;
          digitalWrite(LED, HIGH);
          Serial.println("raw reading overflow");
          break;
        case VL6180X_ERROR_RANGEUFLOW:
          currentAnimation = HOME;
          digitalWrite(LED, HIGH);
          Serial.println("range reading underflow");
          break;
        case VL6180X_ERROR_RANGEOFLOW:
          currentAnimation = HOME;
          digitalWrite(LED, HIGH);
          Serial.println("range reading overflow");
          break;
        default:
          currentAnimation = LIE;
          digitalWrite(LED, HIGH);
          Serial.println("unkown system error");
          break;
        }
      previousMillis = currentMillis;
    }
  }
}

void home() {
  SF0.write(defaultAngle);
  SF1.write(defaultAngle);
  SF2.write(defaultAngle);
  SF3.write(defaultAngle);
  S0.write(stopAngle1);
  S1.write(stopAngle0);
  S2.write(stopAngle1);
  S3.write(stopAngle0);
}

void lie() {
  SF0.write(180);
  SF1.write(180);
  SF2.write(180);
  SF3.write(180);
  S0.write(180);
  S1.write(0);
  S2.write(180);
  S3.write(0);
}

void moveForward() {
  S1.write(0);
  vTaskDelay(500 / portTICK_PERIOD_MS);
  S1.write(30);
  vTaskDelay(10000 / portTICK_PERIOD_MS);
  S1.write(60);
  vTaskDelay(1500 / portTICK_PERIOD_MS);
  S1.write(90);
  vTaskDelay(2000 / portTICK_PERIOD_MS);
  /*SF1.write(defaultAngle+add);
  SF3.write(defaultAngle+add);
  vTaskDelay(500 / portTICK_PERIOD_MS);
  S1.write(stopAngle0-20);
  S3.write(stopAngle0-20);
  vTaskDelay(500 / portTICK_PERIOD_MS);
  SF1.write(defaultAngle);
  SF3.write(defaultAngle);
  vTaskDelay(500 / portTICK_PERIOD_MS);
  SF0.write(defaultAngle+add);
  SF2.write(defaultAngle+add);
  vTaskDelay(500 / portTICK_PERIOD_MS);
  S0.write(stopAngle1+35);
  S2.write(90);
  vTaskDelay(500 / portTICK_PERIOD_MS);
  S1.write(90);
  vTaskDelay(500 / portTICK_PERIOD_MS);
  SF0.write(defaultAngle);
  SF2.write(defaultAngle);
  vTaskDelay(500 / portTICK_PERIOD_MS);
  SF1.write(defaultAngle+add+add);
  vTaskDelay(500 / portTICK_PERIOD_MS);
  S1.write(stopAngle0);
  vTaskDelay(500 / portTICK_PERIOD_MS);
  SF3.write(defaultAngle+10);
  S0.write(90);
  S2.write(stopAngle1);
  vTaskDelay(500 / portTICK_PERIOD_MS);
  SF1.write(defaultAngle);
  vTaskDelay(500 / portTICK_PERIOD_MS);
  SF3.write(defaultAngle);
  /*delay(stopDelay);

  SF0.write(defaultAngle+add);
  SF2.write(defaultAngle+add);
  delay(setSpeed);
  S0.write(stopAngle1+20);
  S2.write(stopAngle1+20);
  delay(setSpeed);
  SF0.write(defaultAngle);
  SF2.write(defaultAngle);
  delay(setSpeed);
  SF1.write(defaultAngle+add);
  SF3.write(defaultAngle+add);
  delay(setSpeed);
  S1.write(stopAngle0-35);
  S3.write(90);
  delay(setSpeed);
  S0.write(90);
  delay(setSpeed);
  SF1.write(defaultAngle);
  SF3.write(defaultAngle);
  delay(setSpeed);
  SF0.write(defaultAngle+add+add);
  delay(setSpeed);
  S0.write(stopAngle1);
  delay(setSpeed);
  SF2.write(defaultAngle+10);
  S1.write(90);
  S3.write(stopAngle0);
  delay(setSpeed);
  SF0.write(defaultAngle);
  delay(setSpeed);
  SF2.write(defaultAngle);
  delay(stopDelay);*/
}

void moveBackward() {
  SF0.write(defaultAngle+add);
  SF2.write(defaultAngle+add);
  delay(1000);
  S0.write(stopAngle1+20);
  S2.write(stopAngle1+20);
  delay(1000);
  SF0.write(defaultAngle);
  SF2.write(defaultAngle);
  delay(1000);
  SF1.write(defaultAngle+add);
  SF3.write(defaultAngle+add);
  delay(1000);
  S3.write(stopAngle0-35);
  S1.write(90);
  delay(1000);
  S2.write(90);
  delay(1000);
  SF1.write(defaultAngle);
  SF3.write(defaultAngle);
  delay(1000);
  SF2.write(defaultAngle+add+add);
  delay(1000);
  S2.write(stopAngle1);
  delay(1000);
  SF0.write(defaultAngle+10);
  S3.write(90);
  S1.write(stopAngle0);
  delay(1000);
  SF0.write(defaultAngle);
  delay(1000);
  SF2.write(defaultAngle);
  /*delay(stopDelay);

  SF1.write(defaultAngle+add);
  SF3.write(defaultAngle+add);
  delay(setSpeed);
  S1.write(stopAngle0-20);
  S3.write(stopAngle0-20);
  delay(setSpeed);
  SF1.write(defaultAngle);
  SF3.write(defaultAngle);
  delay(setSpeed);
  SF0.write(defaultAngle+add);
  SF2.write(defaultAngle+add);
  delay(setSpeed);
  S2.write(stopAngle1+35);
  S0.write(90);
  delay(setSpeed);
  S3.write(90);
  delay(setSpeed);
  SF0.write(defaultAngle);
  SF2.write(defaultAngle);
  delay(setSpeed);
  SF3.write(defaultAngle+add+add);
  delay(setSpeed);
  S3.write(stopAngle0);
  delay(setSpeed);
  SF1.write(defaultAngle+10);
  S2.write(90);
  S0.write(stopAngle1);
  delay(setSpeed);
  SF1.write(defaultAngle);
  delay(setSpeed);
  SF3.write(defaultAngle);
  delay(stopDelay);*/
}

void turnLeft() {
  SF1.write(defaultAngle+add);
  SF3.write(defaultAngle+add);
  delay(setSpeed);
  S1.write(stopAngle0-20);
  S3.write(stopAngle0-20);
  delay(setSpeed);
  SF1.write(defaultAngle);
  SF3.write(defaultAngle);
  delay(setSpeed);
  SF2.write(defaultAngle+add);
  SF0.write(defaultAngle+add);
  delay(setSpeed);
  S0.write(stopAngle1+35);
  S2.write(90);
  delay(setSpeed);
  S1.write(90);
  delay(setSpeed);
  SF2.write(defaultAngle);
  SF0.write(defaultAngle);
  delay(setSpeed);
  SF1.write(defaultAngle+add+add);
  delay(setSpeed);
  S1.write(stopAngle0);
  delay(setSpeed);
  SF3.write(defaultAngle+10);
  S2.write(150);
  S0.write(stopAngle1);
  delay(setSpeed);
  SF1.write(defaultAngle);
  delay(setSpeed);
  SF3.write(defaultAngle);
  delay(stopDelay);

  SF0.write(defaultAngle+add);
  SF2.write(defaultAngle+add);
  delay(setSpeed);
  S0.write(stopAngle1+20);
  S2.write(stopAngle1+20);
  delay(setSpeed);
  SF0.write(defaultAngle);
  SF2.write(defaultAngle);
  delay(setSpeed);
  SF1.write(defaultAngle+add);
  SF3.write(defaultAngle+add);
  delay(setSpeed);
  S3.write(stopAngle0-35);
  S1.write(90);
  delay(setSpeed);
  S2.write(90);
  delay(setSpeed);
  SF1.write(defaultAngle);
  SF3.write(defaultAngle);
  delay(setSpeed);
  SF2.write(defaultAngle+add+add);
  delay(setSpeed);
  S2.write(stopAngle1);
  delay(setSpeed);
  SF0.write(defaultAngle+10);
  S1.write(30);
  S3.write(stopAngle0);
  delay(setSpeed);
  SF2.write(defaultAngle);
  delay(setSpeed);
  SF0.write(defaultAngle);
  delay(stopDelay);
}
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
